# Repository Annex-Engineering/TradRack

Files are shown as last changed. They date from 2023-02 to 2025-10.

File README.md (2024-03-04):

# Trad Rack



Trad Rack is a multimaterial system for FFF printers with a focus on scalability at low cost, developed by Ryan G and the team at Annex Engineering.

Videos of it in action can be found here: 
- [Toolchange and print timelapse (closed beta announcement)](https://youtu.be/wKoVyXH0DT4)
- [Standalone demo (MRRF 2022 preview)](https://youtu.be/hxGiJGAnO-A)

Our discord server can be found here: 

Join me on Discord (https://discord.gg/MzTR3zE)

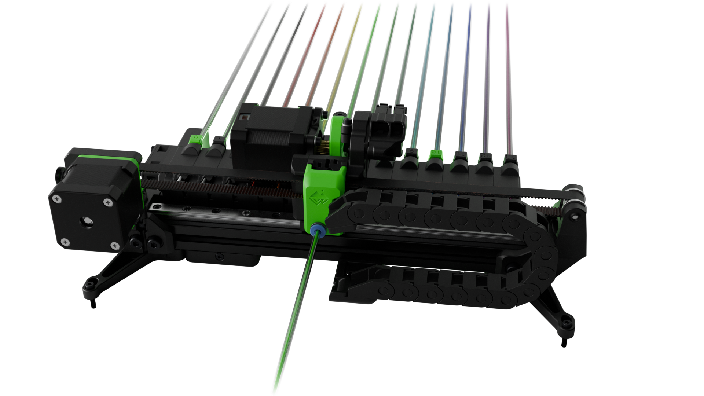
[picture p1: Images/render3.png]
Image of TradRack


## Getting started

See the [Quick Start document](/docs/Quick_Start.md) to get started, or continue
reading below for more general info on Trad Rack.

## Stats

- Single 2020 extrusion as the frame
- Pivoting arm on the selector that lowers a hobbed gear onto the filament, indirectly coupled to a servo through a spring
- MGN9 rail and either 6mm or 9mm 2GT belt for selector movement
- NEMA17 motor for selector movement, and either NEMA17 or 36mm round NEMA14 motor for filament movement

## Scalability

One of the main focuses of Trad Rack is allowing additional filament lanes to be added at the lowest possible cost and assembly/disassembly. Rather than using a separate drive gear (or drive gear pair) for each filament lane, Trad Rack uses a single drive gear pair mounted to the selector for the entire unit. One module is required for each filament lane, and modules can be attached or detached with one screw. Each module consists of the following parts:

- 1X printed module body
- 1X 623 bearing
- 1X M3x8 screw
- 1X M5x10 screw
- 1X M5 T-nut
- 1X bowden fitting

The extrusion, rail, and belt must be long enough to support the selected number of filament lanes, but they can be oversized in order to allow for additional modules to be added later.

## Acknowledgments

- Main filament-switching concept inspired by the [Prusa MMU2](https://github.com/prusa3d/Original-Prusa-i3/tree/MMU2)
- Idea to use a servo to engage/disengage with each filament inspired by the [SMuFF](https://github.com/technik-gegg/SMuFF-1.1)

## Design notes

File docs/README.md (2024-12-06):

# Overview

Welcome to the Trad Rack documentation. If you want to get running as
quickly as possible with minimal reading, see the
[Quick Start document](Quick_Start.md).

## Getting started
- [Quick Start](Quick_Start.md): a step-by-step guide on how to get
  running with Trad Rack.
- [Printer and Hardware Requirements](Printer_and_Hardware_Requirements.md):
  prerequisites for your printer to work with Trad Rack, as well as
  information on other hardware you might need/want to use with Trad
  Rack.

## Assembly and wiring
- [Build Instructions](build_instructions): instructions for
  assembling Trad Rack.
- [Wiring](Wiring.md): information on wiring for Trad Rack.

## Kalico
- [Installation](kalico/Installation.md): how to get Trad Rack set up
  to work with Kalico or Klipper.
- [Config Reference](kalico/Config_Reference.md): config settings for
  Trad Rack.
- [G-Codes](kalico/G-Codes.md): commands added by the trad_rack
  klippy module.
- [Customization](kalico/Customization.md): info on how code is
  divided between the trad_rack klippy module and the config, how to
  customize Trad Rack's behavior through gcode templates, and what the
  trad_rack_optional config file does.
- [Status Reference](kalico/Status_Reference.md): information
  available to macros (and similar) from the trad_rack klippy module.
- [Save Variables](kalico/Save_Variables.md): information on the
  variables that Trad Rack saves to disk using save_variables.

## Tuning and feature overviews
- [Tuning](Tuning.md): overview of the loading and unloading
  processes and information on how to tune them.
- [Tool Mapping](Tool_Mapping.md): info on tool mapping/lane groups
  and how runouts are handled.
- [Tool Naming](Tool_Naming.md): (coming soon)
- [Spoolman Support](Spoolman_Support.md): (coming soon)
- [Extruder Syncing](Extruder_Syncing.md): info on how to use Trad
  Rack as a secondary extruder to reduce load on the printer's main
  extruder, including methods for avoiding error buildup due to
  mismatched extrusion rates.

## Slicing
- [Slicing](slicing/Slicing.md): information on slicing multimaterial
  prints for use with Trad Rack.
- [PrusaSlicer Setup](slicing/PrusaSlicer_Setup.md): instructions for
  using the provided PrusaSlicer profiles, as well as other
  PrusaSlicer-specific slicing info. Make sure to look at the main
  Slicing document first for prerequisites and other info.
- [SuperSlicer Setup](slicing/SuperSlicer_Setup.md): instructions for
  using the provided SuperSlicer profiles, as well as other
  SuperSlicer-specific slicing info. Make sure to look at the main
  Slicing document first for prerequisites and other info.

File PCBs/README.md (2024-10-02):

# TradRack PCBs

The Tradrack-PCBs are a series of PCBs that allow for easier and simpler wiring and troubleshooting on a Trad Rack. They also allow the operator to quickly disconnect the unit from the machine and swap it to another one.

## Boards

| Name | Location |
| --- | --- |
| TR Ebox Distribution | Ebox |
| TR Lower Distribution | Extrusion |
| TR Toolhead | Toolhead |

## Features
The TradRack PCBs have the following features
- 16-pin / 10-pin input/output via MicroFit connector (16-pin to lower distro, 10 pin to toolhead)
- Modular Design
- Dedicated 5V Fused Input (3A Max)
- 1 Aux Expansion ports with power and ground to the Lower Distribution Board
- 3 Aux Expansion ports with power and ground to the Toolhead Board

## Source, PCBs, Gerbers

If you want to help to get the carabiner from any shop that is officially affiliated, please check out the [Annex Sourcing Guide](https://docs.google.com/spreadsheets/d/1O3eyVuQ6M4F03MJSDs4Z71_XyNjXL5HFTZr1jsaAtRc/edit?usp=sharing)

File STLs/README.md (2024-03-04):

# What to print

In general, all parts in the STLs folder need to be printed. However,
there are some exceptions. Some subfolders contain files that you may
not need, and some parts have multiple variants that you can choose
from depending on what hardware you are using.

**Table of Contents**
- [Subfolders that may not be needed](#subfolders-that-may-not-be-needed)
- [STL variants](#stl-variants)
  - [Rail cart variants](#rail-cart-variants)
  - [Belt width variants](#belt-width-variants)
  - [Cable drag chain variants](#cable-drag-chain-variants)

## Subfolders that may not be needed

The following subfolders contain STL files that you may or may not
need to print:

- [Electronics Mounts/Nebula Enclosure](Electronics%20Mounts/Nebula%20Enclosure/):
  these files are only required if you are using the Nebula control
  board. See the
  [Printer and hardware requirements document](/docs/Printer_and_Hardware_Requirements.md#electronics)
  for recommended mounts for other control board options.
- [Electronics Mounts/Base Distribution Board](Electronics%20Mounts/Base%20Distribution%20Board/):
  these files are only required if you are using the optional Trad
  Rack wiring kit.
- [Experimental](Experimental/): experimental parts. These are not
  recommended at this time.
- [Stationary Parts/Numbered Collet Clips](Stationary%20Parts/Numbered%20Collet%20Clips/):
  optional collet clips for labeling the lane modules.
- [Trad Rack Mounts/K3 Side Mount](Trad%20Rack%20Mounts/K3%20Side%20Mount/):
  brackets for mounting Trad Rack to the side of an Annex K3 printer.
  These brackets may also work for mounting Trad Rack to other
  printers or for serving as legs for Trad Rack to sit on a horizontal
  surface. See the
  [Printer and hardware requirements document](/docs/Printer_and_Hardware_Requirements.md#other-recommended-mounts)
  for alternative recommended mounting parts that may work better with
  other printers/setups.

## STL variants

Subfolders containing multiple variants of each part will generally
contain a README file that lists which files you need to print for
each option. The following sections explain file labels that apply to
all STL subfolders in general:

### Rail cart variants

Trad Rack uses an MGN9 rail with either a C-cart or an H-cart. Files
with `(c_cart)` in the filename are only required if using a C-cart.
Files with `(h_cart)` in the filename are only required if using an
H-cart.

### Belt width variants

Trad Rack is compatible with either 6mm or 9mm wide belts (and
pulleys sized for each). Files with `(6mm_belt)` in the filename are
only required if using 6mm wide belts and pulleys/idlers sized for 6mm
belts. Files with `(9mm_belt)` in the filename are only required if
using 9mm wide belts and pulleys/idlers sized for 9mm belts.

### Cable drag chain variants

Cable chains with 10x10mm internal dimensions generally have a 2-hole
mounting pattern for each end, while chains with 10x11mm internal
dimensions generally have a 3-hole mounting pattern. Files with
`(10x10_cable_chain)` in the filename are only required if
using a cable chain with a 2-hole mounting pattern. Files with
`(10x11_cable_chain)` in the filename are only required if using a
cable chain with a 3-hole mounting pattern.

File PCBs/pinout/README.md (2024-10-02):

# Pinout - 16 Pin Harness and 10 Pin Harness

All TR boards (& derivatives) are using a non-standard 16 pin pinout that does not match the carabiner pinout due to alternative power and signaling requirements.

We welcome other groups using the cable for their projects, but kindly ask to note in their project page if they are using the official TR 16 pin pinout, to help prevent damage to users equipment, caused by different pinouts.

## Pinout - 16 Pin Harness

This pinout assumes you're looking directly at the cable. 

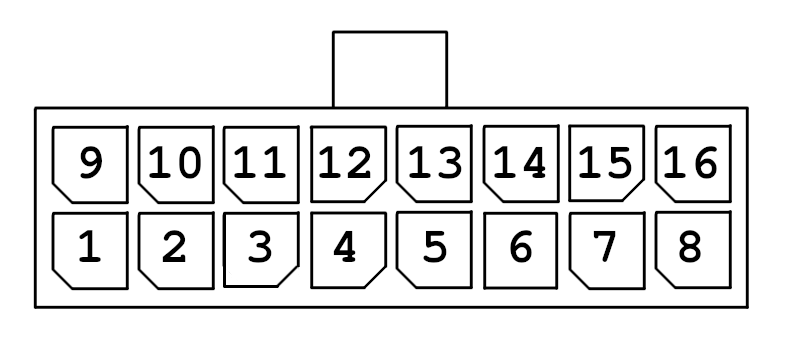
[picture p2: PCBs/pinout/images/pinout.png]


| PinNumber | Usage  | OnPCB | PinNumber | Usage | OnPCB | 
|---|:---:|:---:| --- |:---:|:---:|
| 1  | 5V Input | 5V | 9 | Aux Pin 3 | Aux3
| 2  | Aux Pin 4 | Aux4 | 10 | Aux Pin 2 | Aux2
| 3  | Common Ground | CMN_GND | 11 | Aux Pin 1 | Aux1
| 4  | Feeder End Stop Signal | F_ESTOP_SIGNAL | 12 | Selector End Stop Signal | S_ESTOP_SIGNAL
| 5  | Motor 1 1A | Stepper1A_1 | 13 | Motor 1 2B | Stepper2B_1
| 6  | Motor 1 1B | Stepper1B_1 | 14 | Motor 1 2A | Stepper2A_1
| 7  | Motor 2 1A | Stepper1A_2 | 15 | Motor 2 2B | Stepper2B_2
| 8  | Motor 2 1B | Stepper1B_2 | 16 | Motor 2 2A | Stepper2A_2

## Pinout - 10 Pin Harness

This pinout assumes you're looking directly at the cable. 

| PinNumber | Usage  | OnPCB | PinNumber | Usage | OnPCB | 
|---|:---:|:---:| --- |:---:|:---:|
| 1  | Motor 1 1A | Stepper1A_1 | 6 | Common Ground | CMN_GND 
| 2  | Motor 1 1B | Stepper1B_1 | 7 | 5V Input | 5V
| 3  | Motor 1 2B | Stepper2B_1 | 8 | Aux Pin 3 | Aux3
| 4  | Motor 1 2A | Stepper2A_1 | 9 | Aux Pin 2 | Aux2
| 5  | Feeder End Stop Signal | F_ESTOP_SIGNAL | 10 | Aux Pin 1 | Aux1

## Recommended Wiregauge - 16 Pin Harness

While we have official cables available, we don't want to discourage people making their own cables, as such here is our recommended minimum wiregauge, for making a cable with the official pinout.
These recommendations assume the TR boards are being used in a 50° chamber.

| Pin-Number | Recommended AWG | Recommended mm² |
|:---:|:---:|:---:|
| 1 | 22 | 0.3 |
| 2 | 26 | 0.125 |
| 3 | 22 | 0.3 |
| 4 | 26 | 0.125 |
| 5 | 22 | 0.3 |
| 6 | 22 | 0.3 |
| 7 | 22 | 0.3 |
| 8 | 22 | 0.3 |
| 9 | 26 | 0.125 |
| 10 | 26 | 0.125 |
| 11 | 26 | 0.125 |
| 12 | 26 | 0.125 |
| 13 | 22 | 0.3 |
| 14 | 22 | 0.3 |
| 15 | 22 | 0.3 |
| 16 | 22 | 0.3 |

## Recommended Wiregauge - 10 Pin Harness

While we have official cables available, we don't want to discourage people making their own cables, as such here is our recommended minimum wiregauge, for making a cable with the official pinout.
These recommendations assume the TR boards are being used in a 50° chamber.

| Pin-Number | Recommended AWG | Recommended mm² |
|:---:|:---:|:---:|
| 1 | 22 | 0.3 |
| 2 | 22 | 0.3 |
| 3 | 22 | 0.3 |
| 4 | 22 | 0.3 |
| 5 | 26 | 0.125 |
| 6 | 22 | 0.3 |
| 7 | 22 | 0.3 |
| 8 | 26 | 0.125 |
| 9 | 26 | 0.125 |
| 10 | 26 | 0.125 |

## License

The pinout is licensed under the [MIT license] (https://github.com/git/git-scm.com/blob/main/MIT-LICENSE.txt)

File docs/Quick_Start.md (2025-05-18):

# Quick Start

This document provides an overview of how to get Trad Rack running.
Each section should be completed before moving on to the next.

**Table of Contents**
- [BOM/sourcing and other required hardware](#bomsourcing-and-other-required-hardware)
  - [Item Calculator](#item-calculator)
- [Printing required parts](#printing-required-parts)
- [Mechanical assembly](#mechanical-assembly)
- [Wiring](#wiring)
- [Kalico installation](#kalico-installation)
- [Servo calibration](#servo-calibration)
  - [Servo rotation direction](#servo-rotation-direction)
  - [Servo horn angle](#servo-horn-angle)
  - [Servo up angle](#servo-up-angle)
- [Selector calibration](#selector-calibration)
- [Slicing](#slicing)
- [Changing Slicer\_Unload macro settings](#changing-slicer_unload-macro-settings)
- [First load and unload](#first-load-and-unload)
  - [Setup](#setup)
  - [Loading the toolhead](#loading-the-toolhead)
  - [Unloading the toolhead](#unloading-the-toolhead)
  - [Relevance to print setup](#relevance-to-print-setup)
- [Further reading](#further-reading)

## BOM/sourcing and other required hardware

The bill of materials/sourcing guide for Trad Rack can be found
[here](https://docs.google.com/spreadsheets/d/1SKBtkgSVPqqGEjftI6v6i6T5Bh3Phx-4YXsJYH17ggs/edit?usp=sharing).

Before placing any orders for parts for Trad Rack, it is recommended to read the
[Printer and hardware requirements document](Printer_and_Hardware_Requirements.md)
in case there are any other items you may want to combine into your orders.

### Item Calculator

Several parts of the build are scalable to the needs of the builder. There are two ways to use our item calculator, which can help you determine how many and what sizes of these parts you need.

  - [Web Based Calculator](https://trinket.io/python/694b97d948?outputOnly=true&runOption=run)
  - [Spreadsheet Calculator](https://docs.google.com/spreadsheets/d/1RdqxC5n0PXs8FgdxJVkqQUN2aY69W7eFC76b8XtMozI/edit?usp=sharing)

## Printing required parts

See the following files/folders:

- [Print Settings and File Key](/Print_Settings_and_File_Key.txt):
  print settings to use and info on reading the STL filenames.
- [STLs folder](/STLs): contains all STL files.
- [STLs README](/STLs/README.md): information on what parts to print.

## Mechanical assembly

See the [build instructions](build_instructions) for guidance on
assembling Trad Rack.

> [!TIP]
> An [eDrawing](/eDrawings/) is also available if you want to view a
> 3D model of Trad Rack. You will need
> [eDrawings Viewer](https://www.edrawingsviewer.com/) to open this
> file. If you are using the Nebula control board, a separate eDrawing
> is also available for help on assembling its enclosure.

## Wiring

See the [Wiring document](Wiring.md).

## Kalico installation

See the [Kalico installation document](kalico/Installation.md).

## Servo calibration

This section involves setting the rotation direction and angles of the
servo. You will need to have Trad Rack fully assembled, wired, and
connected to your printer with Kalico running.

To prepare, remove the servo from Trad Rack by undoing the 2 screws
that attach it to the right carriage.

### Servo rotation direction

Run the following gcode command:

```
TR_SERVO_UP
```

Then run the following gcode command, and this time observe the motion
of the servo. When viewed from the front of the servo spline, the 
servo should rotate clockwise:
    
```
TR_SERVO_DOWN FORCE=1
```

If the servo rotated clockwise, you can continue on to setting the
[servo horn angle](#servo-horn-angle). Otherwise, in your Kalico
config, swap the values of `servo_down_angle` and `servo_up_angle` in
the [trad_rack] section. Then restart Kalico and continue.

### Servo horn angle

Run the following gcode command:

```
TR_SERVO_DOWN FORCE=1
```

Loosen the screw in the center of the servo horn and the screw in
the clamp.

For this section, you will need the servo jig that has "HORN ANGLE"
written on the side:

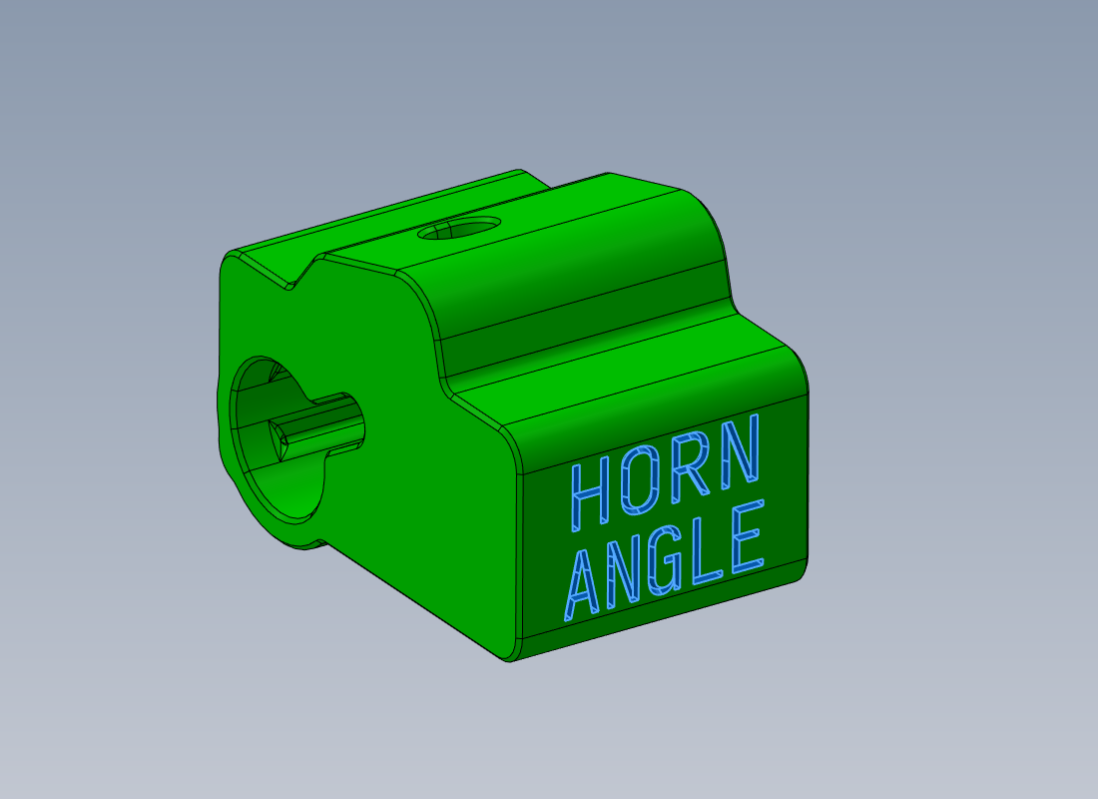
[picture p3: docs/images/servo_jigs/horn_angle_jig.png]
HORN ANGLE servo jig


Insert the servo into the servo jig. You may need to rotate the
servo horn around the servo spline by hand so that it is at the
correct angle for the bearing to fit into the jig. The servo's wires
should be exiting to the left to match the orientation in the image:

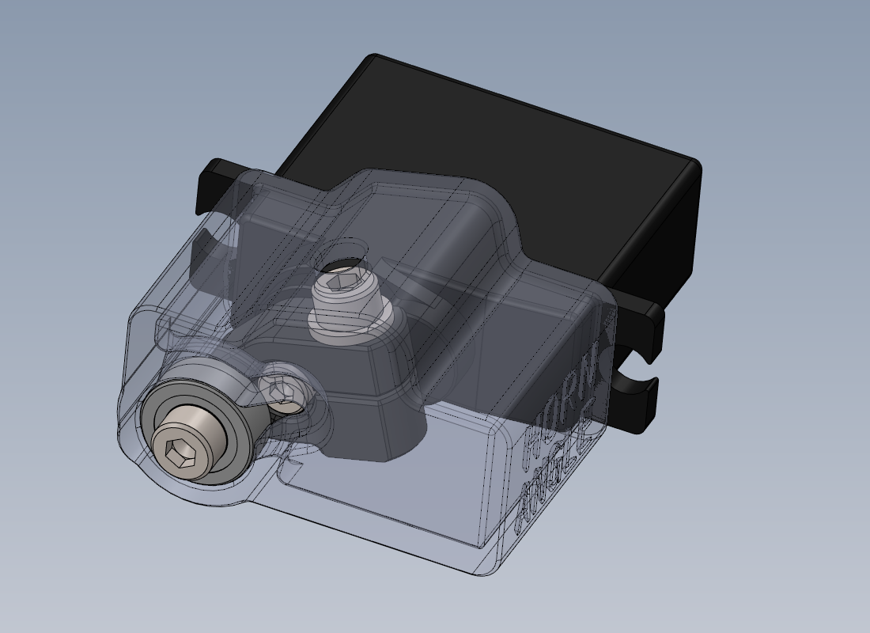
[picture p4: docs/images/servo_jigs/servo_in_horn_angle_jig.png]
Servo in HORN ANGLE jig


Tighten the two screws you loosened earlier. Then remove the servo
jig.

### Servo up angle

For this section, you will need the servo jig that has "UP ANGLE"
written on the side:

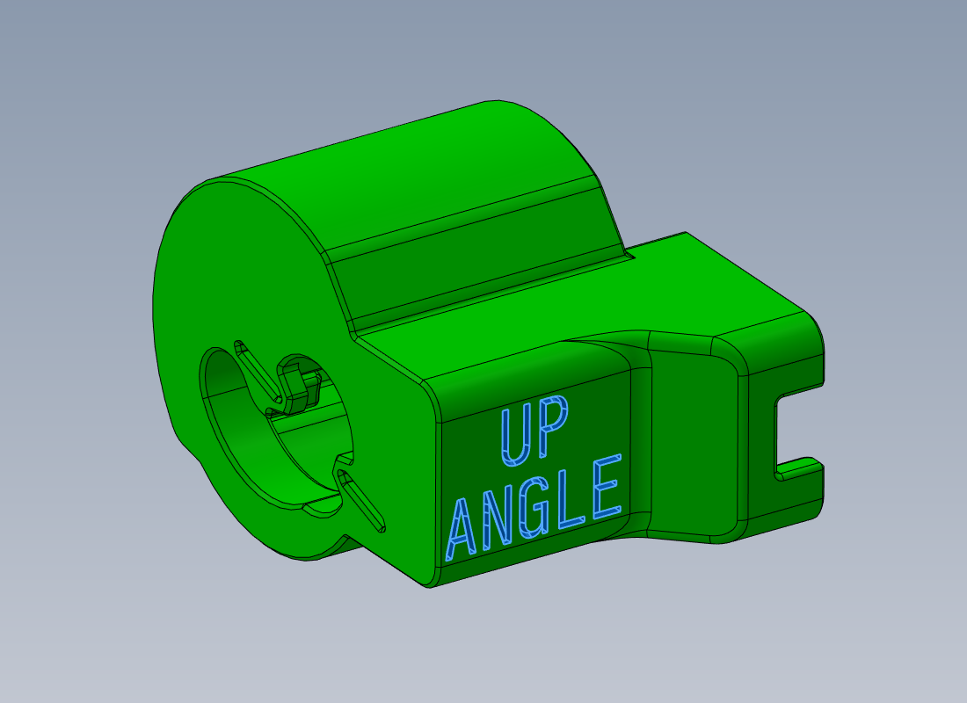
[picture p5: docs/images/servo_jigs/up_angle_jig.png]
UP ANGLE servo jig


Insert the servo into the servo jig. The servo's wires should be
exiting to the left to match the orientation in the image:

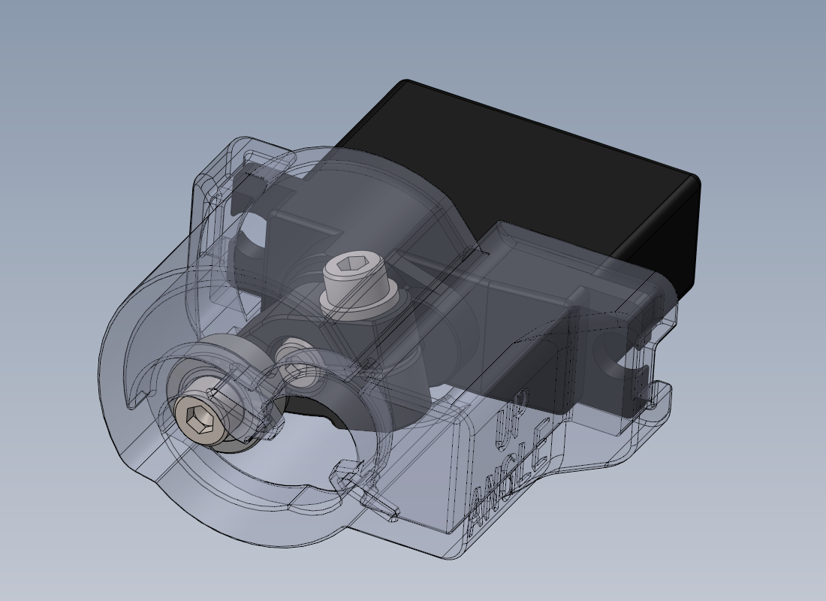
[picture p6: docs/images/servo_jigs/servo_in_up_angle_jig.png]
Servo in UP ANGLE jig


Run the following gcode command. Observe the "commanded angle" that is
reported in the console:

```
TR_SERVO_TEST
```

Look at the front of the servo jig and check the position of the screw
in the bearing relative to the slots. The goal of this section is
to get the screw close to lining up with the slots:

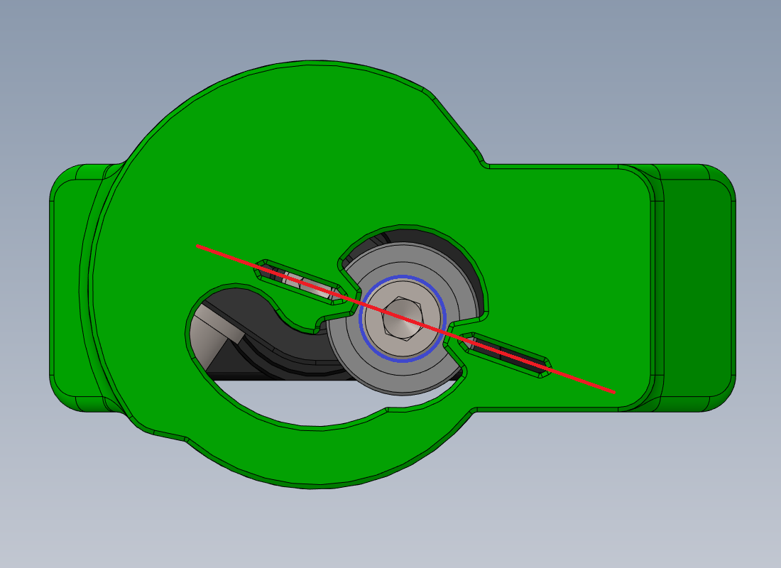
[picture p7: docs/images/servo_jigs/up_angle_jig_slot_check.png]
UP ANGLE servo jig slot check


There is a range of acceptable angles, and the screw does not
have to exactly align with the slots. If the servo angle is within the
target range, the jig will be able to slide far enough over the servo
that the screw protrudes from the front of the jig:

| Wrong angle (screw can't protrude) | Angle within target range (screw protrudes) |
| --- | --- |
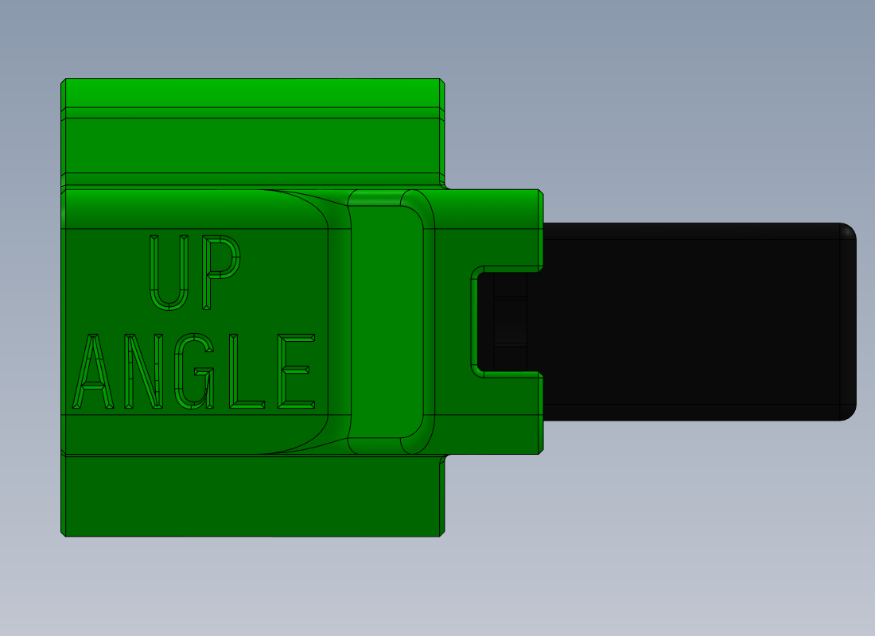
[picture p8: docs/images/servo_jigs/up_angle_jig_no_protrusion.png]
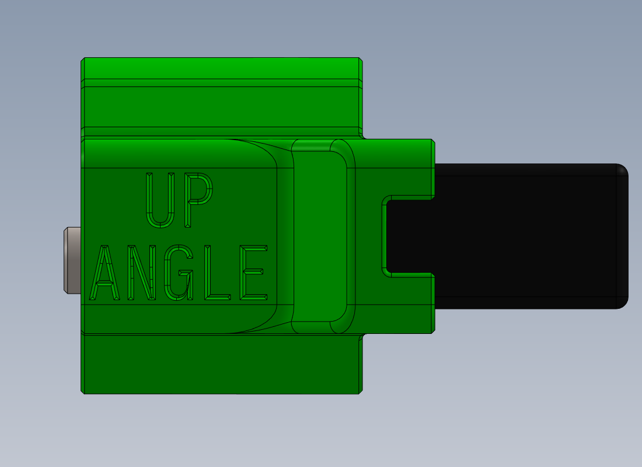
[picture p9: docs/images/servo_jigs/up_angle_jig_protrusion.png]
|   |   |

If the jig is blocked from being able to slide far enough for the
screw to protrude, you will need to try another angle. Use the
following command to test a specific angle. The "commanded angle" from
earlier corresponds to the current angle of the servo. A higher angle
will turn the servo counterclockwise, and a lower angle will turn it
clockwise:

```
TR_SERVO_TEST ANGLE=<angle>
```

Repeat with different angles as necessary until the servo is 
within the target range.

Once the servo aligns well enough with the slots that the screw can
protrude from the jig, observe the last "raw angle" value reported in
the console. In your main Trad Rack config file, replace the value of
`servo_up_angle` in the [trad_rack] section with the "raw angle"
value. Remove the servo jig and restart Kalico. Then run the
following gcode command:

```
TR_SERVO_DOWN FORCE=1
```

Finally, reattach the servo to Trad Rack.

## Selector calibration

This section involves calibrating `lane_spacing`, as well as the min,
endstop, and max positions of the selector motor. You will need access
to filament (either a spool or a short piece is fine).

Run the following gcode command and follow the instructions in the
console:

```
TR_CALIBRATE_SELECTOR
```

When the calibration finishes and you are prompted to do so, replace
the values in your main Trad Rack config file with the new values
for the following:

- in [trad_rack]:
  - `lane_spacing`
- in [stepper_tr_selector]:
  - `position_min`
  - `position_endstop`
  - `position_max`

## Slicing

See the [Slicing document](slicing/Slicing.md).

## Changing Slicer_Unload macro settings

This section involves adjusting the settings of the
[Slicer_Unload macro](kalico/Customization.md#tip-shaping) to match
your slicer settings so that toolhead unloads performed outside of a
print will closely match toolhead unloads performed during a print.

Under `[gcode_macro Slicer_Unload]` in your copy of
[trad_rack_optional.cfg](/Kalico/kalico_config/trad_rack_optional.cfg),
change the values of the following variables to match the values you
set in the slicer profile. Variable names match the "parameter names"
used in the slicer config files:

- all variables under the comment `# printer settings`
- all variables under the comment `# filament settings`

In addition, if you are using SuperSlicer, do the same for all
variables under the comment `# filament settings only in SuperSlicer`.

Set `variable_superslicer` to `True` if you are using SuperSlicer. If
you are using PrusaSlicer or OrcaSlicer, set it to `False`.

Optional: if you want to use different tip-shaping settings for
different filaments (when unloading the toolhead outside of a print),
you can define presets in `[gcode_macro Set_Slicer_Unload_Preset]` in
the same file. See the comments in the macro and the example preset
variables for reference.

## First load and unload

This section goes through the process of running your first toolhead
load and unload to test Trad Rack.

### Setup

Run the following command to home Trad Rack's selector:

```
TR_HOME
```

Get a filament spool ready to feed into Trad Rack. Then run the
following command, and insert the filament into lane module 0 when
prompted to do so in the console:

```
TR_LOAD_LANE LANE=0
```

Trad Rack should now have a filament loaded into lane module 0.

### Loading the toolhead

To load the toolhead from tool 0 (which starts with lane 0 as its
default lane*), run the following command:

```
T0
```

\* see the [G-Codes document](kalico/G-Codes.md#tr_load_toolhead)
for more details on the available parameters for the `TR_LOAD_TOOLHEAD`
and `T<tool index>` toolchange commands.

Depending on your `hotend_load_length` value, filament may or may not
come out of the nozzle.[^1] For the sake of this test, run the
following commands to ensure filament comes out of the nozzle:

```
M83
G1 E10
```

[^1]: It is recommended to set `hotend_load_length` to a value small
enough that filament does not ooze out directly after calling the
toolchange command so that you do not get a blob on the wipe tower.
However, it should not be so small that there are large gaps in the
wipe tower.

### Unloading the toolhead

Run the following command to unload the toolhead. Trad Rack
should retract the filament back into lane module 0:

```
TR_UNLOAD_TOOLHEAD
```

### Relevance to print setup

Congrats, you have completed your first load and unload with Trad
Rack!

When printing with Trad Rack, make sure to load all the filaments you
might need into their lane modules beforehand using the `TR_LOAD_LANE`
command (after ensuring Trad Rack's selector is homed using `TR_HOME`
as needed). It is also possible to load filaments into the lane
modules completely by hand without any gcode commands, but this is
generally not recommended since you will need to make sure the
filament tip is pushed far enough forward that Trad Rack can grab it
but not so far that it blocks selector movement.

It is up to you whether or not to load the first filament to the
toolhead (using `T<tool index>` or `TR_LOAD_TOOLHEAD` commands)
before starting a print. Either way works, as the start gcode in the
slicer will ensure that the first filament gets loaded if it isn't
already.

Whenever you need to unload filament from the toolhead, you can use
the `TR_UNLOAD_TOOLHEAD` command. If a filament is currently loaded
and you want to load a different one, you do not have to call
`TR_UNLOAD_TOOLHEAD` before calling a toolchange command (either
`T<tool index>` or `TR_LOAD_TOOLHEAD`) to load the next filament since
the toolchange command will automatically include the unload as
needed.

## Further reading

This marks the end of the required steps to get Trad Rack running.
See the [Overview document](README.md) to see the full list of
documents available. Some of these were already linked in this guide,
but there are additional ones that provide more information on what
values can be changed for fine tuning, what gcode commands are
available, etc.

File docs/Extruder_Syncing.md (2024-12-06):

# Extruder Syncing

Extruder syncing is an optional feature that syncs Trad Rack's
filament driver to the extruder during printing, as well as during any
extrusion moves within toolhead loading or unloading that would
normally involve only the extruder. It is highly recommended to use
this feature in conjunction with a
[Belay sensor](#belay-extruder-sync-sensor) rather than by itself.

**Table of Contents**
- [Purpose](#purpose)
- [Belay (extruder sync sensor)](#belay-extruder-sync-sensor)
- [Enabling extruder syncing](#enabling-extruder-syncing)

## Purpose

Long filament paths, buffers, or very heavy spools can cause extra resistance
in filament movement, potentially causing the printer's extruder to
struggle. One solution is to use Trad Rack as a secondary extruder in
series with the primary extruder to take some of the load. With
extruder syncing enabled, Trad Rack's filament driver motor is synced
to the primary extruder.

## Belay (extruder sync sensor)

By default, with extruder syncing enabled Trad Rack's filament driver
will be directly synced to the primary extruder. It is not recommended
to use extruder syncing in this way without a sensor since Trad Rack's
filament driver and the primary extruder may gradually drift out of
sync during a long print with no toolchanges or very long extrusion
distances between toolchanges.

The [Belay sensor][1] solves this problem by dynamically
adjusting the `rotation_distance` setting of Trad Rack's filament
driver to keep it in sync with the primary extruder. See
[the Belay repository][1] for details.

[1]: https://github.com/Annex-Engineering/Belay

## Enabling extruder syncing

To enable extruder syncing, set `sync_to_extruder` to `True` in the
[trad_rack config section](kalico/Config_Reference.md#trad_rack).
The [TR_SYNC_TO_EXTRUDER gcode command](kalico/G-Codes.md#tr_sync_to_extruder)
can also be used to enable syncing, and
[TR_UNSYNC_FROM_EXTRUDER](kalico/G-Codes.md#tr_unsync_from_extruder)
can be used to disable syncing. However, any changes made by these
gcode commands will not persist across restarts.

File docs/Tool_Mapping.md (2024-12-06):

# Tool Mapping

This document contains info on tool mapping/lane groups and how
runouts are handled.

By default, each tool or extruder number specified in gcode
corresponds to a lane module on Trad Rack. However, tool numbers can
be decoupled from lane numbers. This allows reassigning a lane to a
tool with a different number and/or assigning a group of lanes to the
same tool.

**Table of Contents**
- [Use cases](#use-cases)
  - [Chaining identical spools together](#chaining-identical-spools-together)
  - [Remapping right before a print](#remapping-right-before-a-print)
- [Slicer and gcode](#slicer-and-gcode)
- [Runouts](#runouts)

## Use cases

Tool mapping has a couple use cases:

### Chaining identical spools together

If you have multiple identical spools of filament, you may want to
swap from one to the next each time one runs out during a print. This
can be accomplished by feeding each spool into a different lane module
in Trad Rack and assigning each of these lanes to the same tool so
that Trad Rack will recognize that they are interchangeable. When
filament from one lane runs out, Trad Rack will automatically initiate
a toolchange to filament from another lane that is assigned to the
same tool, and it will continue the print.

Since you can have as many tools/lane groups as you want (up to the
number of lanes), you can use up old spools while still being able to
print with multiple colors/materials.

### Remapping right before a print

If you already have filaments loaded into Trad Rack and you want to
run a print file that you sliced previously, you don't have to be
restricted to using the same color/material order as what is defined
in the gcode. The tool numbers match the order defined in the gcode,
but you can map whichever lane(s) you want to each tool so that the
correct filament is used for each part of the print.

## Slicer and gcode

The slicer does not need to be aware of the lane groups; it only
tells Trad Rack which tool needs to be loaded. Extruder numbers in the
slicer correspond directly to tool numbers.

Each tool has a default lane that is loaded with every
`TR_LOAD_TOOLHEAD TOOL=<tool index>` or `T<tool index>` command.
Whenever the filament from one lane runs out, another lane in the
tool's lane group will become the new default lane. In addition, if
you load the toolhead with filament from a specific lane using
`TR_LOAD_TOOLHEAD LANE=<lane index>`, that lane will become the new
default lane for its assigned tool.
[Several gcode commands](kalico/G-Codes.md#tool-mapping) are
available for viewing and manipulating the tool mapping/lane
groups.

## Runouts

Whenever Trad Rack detects that the filament has run out (via the
selector filament sensor), it will pause the print, unload the current
filament, and attempt to load new filament from a lane assigned to the
same tool. If successful, it will resume the print automatically. If
unsuccessful, a message will be sent to the console prompting the user
to take action and resume the print manually.

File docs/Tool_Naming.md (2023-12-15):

# Tool Naming

Coming soon. See the `work-name-groups-and-spoolman` branch.

This feature will allow assigning names to tools. Optionally,
toolchanges can be initiated by selecting a name rather than a tool
or lane. For example, the filament profile name in the slicer could
be passed as the name in the toolchange command so that the order of
extruders in the slicer and the order in which filaments are loaded
into trad rack will not matter (as long as the same name is assigned
to a tool). This feature may later tie into
[Spoolman support](Spoolman_Support.md) for automatically assigning
names to tools when a spool ID is assigned to a lane.

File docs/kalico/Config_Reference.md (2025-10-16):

# Trad Rack Configuration reference

This document is modeled after Kalico's
[Config Reference document](https://docs.kalico.gg/Config_Reference.html)
but only contains items pertaining to Trad Rack.

**Table of Contents**
- [Main configuration](#main-configuration)
  - [\[trad\_rack\]](#trad_rack)
- [Additional sections](#additional-sections)
  - [\[stepper\_tr\_selector\]](#stepper_tr_selector)
  - [\[stepper\_tr\_fil\_driver\]](#stepper_tr_fil_driver)
  - [\[tmc2209 stepper\_tr\_selector\]](#tmc2209-stepper_tr_selector)
  - [\[tmc2209 stepper\_tr\_fil\_driver\]](#tmc2209-stepper_tr_fil_driver)
  - [\[servo tr\_servo\]](#servo-tr_servo)

## Main configuration

### [trad_rack]

Main configuration section for Trad Rack. Some config options
reference [Tuning.md](/docs/Tuning.md) for more details.
```
[trad_rack]
selector_max_velocity:
#   Maximum velocity (in mm/s) of the selector. 
#   This parameter must be specified.
selector_max_accel:
#   Maximum acceleration (in mm/s^2) of the selector. 
#   This parameter must be specified.
#filament_max_velocity:
#   Maximum velocity (in mm/s) for filament movement. 
#   Defaults to buffer_pull_speed.
#filament_max_accel: 1500.0
#   Maximum acceleration (in mm/s^2) for filament movement.
#   The default is 1500.0.
toolhead_fil_sensor_pin:
#   The pin on which the toolhead filament sensor is connected.
#   If a pin is not specified, no toolhead filament sensor will 
#   be used.
lane_count:
#   The number of filament lanes. This parameter must be specified.
lane_spacing:
#   Spacing (in mm) between filament lanes. 
#   This parameter must be specified.
#lane_offset_<lane index>:
#   Options with a "lane_offset_" prefix may be specified for any of
#   the lanes (from 0 to lane_count - 1). The option will apply an
#   offset (in mm) to the corresponding lane's position. Lane offsets
#   do not affect the position of any lanes besides the one specified
#   in the option name. This option is intended for fine adjustment
#   of each lane's position to ensure that the filament paths in the
#   lane module and selector line up with each other.
#   The default is 0.0 for each lane.
#lane_spacing_mod_<lane index>:
#   Options with a "lane_spacing_mod_" prefix may be specified for any
#   of the lanes (from 0 to lane_count - 1). The option will apply an
#   offset (in mm) to the corresponding lane's position, as well as
#   any lane with a higher index. For example, if lane_spacing_mod_2
#   is 4.0, any lane with an index of 2 or above will have its
#   position increased by 4.0. This option is intended to account for
#   variations in a lane module that will affect its position as well
#   as the positions of any subsequent modules with a higher index.
#   The default is 0.0 for each lane.
servo_down_angle:
#   The angle (in degrees) for the servo's down position.
#   This parameter must be specified.
servo_up_angle:
#   The angle (in degrees) for the servo's up position.
#   This parameter must be specified.
#servo_wait_ms: 500
#   Time (in milliseconds) to wait for the servo to complete moves
#   between the up and down angles. The default is 500.
selector_unload_length:
#   Length (in mm) to retract a piece of filament out of the selector
#   and back into the lane module after the selector sensor has been
#   triggered or untriggered. This parameter must be specified.
#selector_unload_length_extra: 0.0
#   Extra length (in mm) that is added to selector_unload_length when
#   retracting a piece of filament out of the selector and back into
#   the lane module. After the retraction, the filament is moved
#   forward by this length as well (so this option's value has no
#   effect on the final position of the filament). This option may be
#   useful when using Trad Rack with a motorized spool rewinder that
#   senses tension or compression in the filament between the spool
#   and Trad Rack in order to determine when to rotate the spool. The
#   extra forward movement of the filament after retracting is
#   intended to force the rewinder's sensor to detect tension in the
#   filament, causing rewinding to cease immediately so the filament
#   tip is not moved out of position by excess spool movement. The
#   default is 0.0.
#eject_length: 10.0
#   Length (in mm) to eject the filament into the lane module past the
#   length defined by selector_unload_length. The filament is ejected
#   whenever unloading a depleted spool after a runout to make sure
#   that filament segment is not loaded again until it has been
#   replaced.
bowden_length:
#   Length (in mm) to quickly move filament through the bowden tube
#   between Trad Rack and the toolhead during loads and unloads.
#   See Tuning.md for details. This parameter must be specified.
extruder_load_length:
#   Length (in mm) to move filament into the extruder when loading the
#   toolhead. See Tuning.md for details.
#   This parameter must be specified.
hotend_load_length:
#   Length (in mm) to move filament into the hotend when loading the
#   toolhead. See Tuning.md for details.
#   This parameter must be specified.
toolhead_unload_length:
#   Length (in mm) to move filament out of the toolhead during an
#   unload. See Tuning.md for details. If toolhead_fil_sensor_pin is
#   specified, this parameter must be specified.
#   If toolhead_fil_sensor_pin is not specified, the default is
#   extruder_load_length + hotend_load_length.
#selector_sense_speed: 40.0
#   Speed (in mm/s) when moving filament until the selector
#   sensor is triggered or untriggered. See Tuning.md for details
#   on when this speed is applied. The default is 40.0.
#selector_unload_speed: 60.0
#   Speed (in mm/s) to move filament when unloading the selector.
#   The default is 60.0.
#eject_speed: 80.0
#   Speed (in mm/s) to move the filament when ejecting a filament
#   segment into the lane module.
#spool_pull_speed: 100.0
#   Speed (in mm/s) to move filament through the bowden tube when
#   loading from a spool. See Tuning.md for details. 
#   The default is 100.0.
#buffer_pull_speed:
#   Speed (in mm/s) to move filament through the bowden tube when
#   unloading or loading from a buffer. See Tuning.md for details.
#   Defaults to spool_pull_speed.
#toolhead_sense_speed:
#   Speed (in mm/s) when moving filament until the toolhead
#   sensor is triggered or untriggered. See Tuning.md for details on
#   when this speed is applied. Defaults to selector_sense_speed.
#extruder_load_speed:
#   Speed (in mm/s) to move filament into the extruder when loading
#   the toolhead. See Tuning.md for details. The default is 60.0.
#hotend_load_speed:
#   Speed (in mm/s) to move filament into the hotend when loading the
#   toolhead. See Tuning.md for details. The default is 7.0.
#toolhead_unload_speed:
#   Speed (in mm/s) to move filament when unloading the toolhead.
#   See Tuning.md for details. Defaults to extruder_load_speed.
#load_with_toolhead_sensor: True
#   Whether to use the toolhead sensor when loading the toolhead.
#   See Tuning.md for details. Defaults to True but is ignored if
#   toolhead_fil_sensor_pin is not specified. 
#unload_with_toolhead_sensor: True
#   Whether to use the toolhead sensor when unloading the toolhead.
#   See Tuning.md for details. Defaults to True but is ignored if
#   toolhead_fil_sensor_pin is not specified.
#fil_homing_retract_dist: 20.0
#   Distance (in mm) to retract filament away from a filament sensor
#   before moving on to the next move. This retraction occurs whenever
#   a filament sensor is triggered early during a fast move through
#   the bowden tube. See Tuning.md for details. The default is 20.0.
#target_toolhead_homing_dist:
#   Target filament travel distance (in mm) when homing to the
#   toolhead filament sensor during a load. See Tuning.md for details.
#   Defaults to either 10.0 or toolhead_unload_length, whichever is
#   greater.
#target_selector_homing_dist:
#   Target filament travel distance (in mm) when homing to the
#   selector filament sensor during an unload. See Tuning.md for
#   details. The default is 10.0.
#bowden_length_samples: 10
#   Maximum number of samples that are averaged to set bowden lengths
#   for loading and unloading. See Tuning.md for details. The default
#   is 10.
#load_lane_time: 15
#   Approximate maximum time (in seconds) to wait for filament to
#   reach the selector filament sensor when loading a lane with the
#   TR_LOAD_LANE gcode command. This time starts when the user is
#   prompted to insert filament and determines when the command will
#   be halted early if no filament is detected. The default is 15.
#load_selector_homing_dist:
#   Maximum distance to try to move filament when loading from a lane
#   module to the selector filament sensor before halting the homing
#   move. This value is not used by the TR_LOAD_LANE command but is
#   used in similar scenarios that do not involve user interaction.
#   Defaults to selector_unload_length * 2.
#bowden_load_homing_dist:
#   Maximum distance to try to move filament near the end of a
#   toolhead load (during the slow homing move to the toolhead sensor)
#   before halting the homing move. Defaults to bowden_length.
#bowden_unload_homing_dist:
#   Maximum distance to try to move filament near the end of a
#   toolhead unload (during the slow homing move to the selector
#   sensor) before halting the homing move. Defaults to bowden_length.
#unload_toolhead_homing_dist:
#   Maximum distance to try to move filament near the beginning of a
#   toolhead unload (during the homing move to the toolhead sensor)
#   before halting the homing move.
#   Defaults to (extruder_load_length + hotend_load_length) * 2.
#sync_to_extruder: False
#   Syncs Trad Rack's filament driver to the extruder during printing,
#   as well as during any extrusion moves within toolhead loading or
#   unloading that would normally involve only the extruder.
#   The default is False.
#user_wait_time: 15
#   Time (in seconds) to wait for the user to take an action
#   before continuing automatically. If set to -1, Trad Rack will wait
#   for the user indefinitely. This value is currently used by the
#   TR_LOCATE_SELECTOR gcode command. The default is 15.
#register_toolchange_commands: True
#   Whether to register gcode commands T0, T1, T2, etc. so that they
#   can be used to initiate toolchanges with Trad Rack. If set to
#   False, the TR_LOAD_TOOLHEAD command can still be used as a
#   substitute to initiate toolchanges. The default is True.
#save_active_lane: True
#   Whether to save the active lane to disk whenever it is set using
#   save_variables. If set to True, the TR_LOCATE_SELECTOR gcode
#   command will infer the active lane if the selector filament sensor
#   is triggered and an active lane was saved previously.
#   The default is True.
#keep_servo_down_after_lane_load: False
#   If set to True, after loading filament into a lane the servo is
#   kept down to hold the filament in place. The default is False.
#minimum_cruise_ratio: 0.0
#   See the "printer" section of Kalico's Config Reference document
#   for a description of this parameter. This parameter affects
#   selector moves and filament moves made by Trad Rack. The default
#   is 0.0.
#square_corner_velocity: 0.0
#   See the "printer" section of Kalico's Config Reference document
#   for a description of this parameter. This parameter can affect
#   selector moves and filament moves made by Trad Rack. The default
#   is 0.0.
#log_bowden_lengths: False
#   Whether to log bowden load length data and bowden unload length
#   data (to ~/bowden_load_lengths.csv and ~/bowden_unload_lengths.csv
#   respectively). The default is False.
#pre_unload_gcode:
#   Gcode command template that is run before the toolhead is
#   unloaded. The default is to run no extra commands.
#post_unload_gcode:
#   Gcode command template that is run after the toolhead is
#   unloaded. The default is to run no extra commands.
#pre_load_gcode:
#   Gcode command template that is run before the toolhead is
#   loaded. The default is to run no extra commands.
#post_load_gcode:
#   Gcode command template that is run after the toolhead is
#   loaded. The default is to run no extra commands.
#pause_gcode:
#   Gcode command template that is run whenever Trad Rack needs to
#   pause the print (usually due to a failed load or unload). The
#   default is to run the PAUSE gcode command.
#resume_gcode:
#   Gcode command template that is run whenever the TR_RESUME command
#   needs to resume the print. The default is to run the RESUME
#   gcode command.
```

## Additional sections

### [stepper_tr_selector]

Section for the stepper that moves the selector between lanes.

```
[stepper_tr_selector]
step_pin:
dir_pin:
enable_pin:
rotation_distance:
microsteps:
full_steps_per_rotation:
endstop_pin:
position_min:
position_endstop:
position_max:
#   This should be set to (lane_count - 1) * lane_spacing.
homing_speed:
#   See the "stepper" section in Kalico's Config_Reference.md
#   document for a description of the above parameters.
```

### [stepper_tr_fil_driver]

Section for the stepper that moves filament.

```
[stepper_tr_fil_driver]
step_pin:
dir_pin:
enable_pin:
rotation_distance:
gear_ratio:
microsteps:
full_steps_per_rotation:
endstop_pin:
position_min:
#   This should be set to a large negative number with an absolute
#   value greater than the length of the bowden tube between Trad Rack
#   and the toolhead.
position_endstop: 0
position_max:
#   This should be set to a large positive number greater than the
#   length of the bowden tube between Trad Rack and the toolhead.
homing_positive_dir: False
#   See the "[stepper]" section in Kalico's Config_Reference.md
#   document for a description of the above parameters.
```

### [tmc2209 stepper_tr_selector]

Stepper driver section for stepper_tr_selector.

```
[tmc2209 stepper_tr_selector]
uart_pin:
run_current:
sense_resistor:
#   See the "[tmc_2209]" section in Kalico's Config_Reference.md
#   document for a description of the above parameters. You may have
#   to use a different section name if you use a different driver.
```

### [tmc2209 stepper_tr_fil_driver]

Stepper driver section for stepper_tr_fil_driver.

```
[tmc2209 stepper_tr_selector]
uart_pin:
run_current:
sense_resistor:
#   See the "[tmc_2209]" section in Kalico's Config_Reference.md
#   document for a description of the above parameters. You may have
#   to use a different section name if you use a different driver.
```

### [servo tr_servo]

Section for the servo that moves the drive gear up and down.

```
[servo tr_servo]
pin:
maximum_servo_angle:
minimum_pulse_width:
maximum_pulse_width:
#   See the "[servo]" section in Kalico's Config_Reference.md
#   document for a description of the above parameters.
```

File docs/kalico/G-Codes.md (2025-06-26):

# G-Codes

This document is modeled after Kalico's
[G-Codes document](https://docs.kalico.gg/G-Codes.html) but only
contains items pertaining to Trad Rack.

**Table of Contents**
- [General commands](#general-commands)
  - [TR\_HOME](#tr_home)
  - [TR\_GO\_TO\_LANE](#tr_go_to_lane)
  - [TR\_LOAD\_LANE](#tr_load_lane)
  - [TR\_LOAD\_TOOLHEAD](#tr_load_toolhead)
  - [T0, T1, T2, etc.](#t0-t1-t2-etc)
  - [TR\_UNLOAD\_TOOLHEAD](#tr_unload_toolhead)
  - [TR\_SERVO\_DOWN](#tr_servo_down)
  - [TR\_SERVO\_UP](#tr_servo_up)
  - [TR\_SET\_ACTIVE\_LANE](#tr_set_active_lane)
  - [TR\_RESET\_ACTIVE\_LANE](#tr_reset_active_lane)
  - [TR\_RESUME](#tr_resume)
  - [TR\_LOCATE\_SELECTOR](#tr_locate_selector)
  - [TR\_NEXT](#tr_next)
  - [TR\_SYNC\_TO\_EXTRUDER](#tr_sync_to_extruder)
  - [TR\_UNSYNC\_FROM\_EXTRUDER](#tr_unsync_from_extruder)
- [Calibration and testing](#calibration-and-testing)
  - [TR\_SERVO\_TEST](#tr_servo_test)
  - [TR\_CALIBRATE\_SELECTOR](#tr_calibrate_selector)
  - [TR\_SET\_HOTEND\_LOAD\_LENGTH](#tr_set_hotend_load_length)
  - [TR\_DISCARD\_BOWDEN\_LENGTHS](#tr_discard_bowden_lengths)
- [Tool mapping](#tool-mapping)
  - [TR\_ASSIGN\_LANE](#tr_assign_lane)
  - [TR\_SET\_DEFAULT\_LANE](#tr_set_default_lane)
  - [TR\_RESET\_TOOL\_MAP](#tr_reset_tool_map)
  - [TR\_PRINT\_TOOL\_MAP](#tr_print_tool_map)
  - [TR\_PRINT\_TOOL\_GROUPS](#tr_print_tool_groups)
- [Macros](#macros)

## General commands

### TR_HOME
`TR_HOME`: Homes the selector.

### TR_GO_TO_LANE
`TR_GO_TO_LANE LANE=<lane index>`: Moves the selector to the specified
lane.

### TR_LOAD_LANE
`TR_LOAD_LANE LANE=<lane index> [RESET_SPEED=<0|1>]`: Ensures filament
is loaded into the module for the specified lane by prompting the user
to insert filament, loading filament from the module into the
selector, and retracting the filament back into the module.
If RESET_SPEED is 1, the bowden move speed used for the
specified LANE will be reset to spool_pull_speed from the
[trad_rack config section](Config_Reference.md#trad_rack)
(see [bowden speeds](/docs/Tuning.md#bowden-speeds) for details on how
the bowden speed settings are used). If not specified, RESET_SPEED
defaults to 1.

### TR_LOAD_TOOLHEAD
`TR_LOAD_TOOLHEAD LANE=<lane index>|TOOL=<tool index>
[MIN_TEMP=<temperature>] [EXACT_TEMP=<temperature>]
[BOWDEN_LENGTH=<mm>] [EXTRUDER_LOAD_LENGTH=<mm>]
[HOTEND_LOAD_LENGTH=<mm>]`: Loads filament from the specified lane or
tool into the toolhead*. Either LANE or TOOL must be specified. If
both are specified, then LANE takes precedence. If there is already an
"active lane" because the toolhead has been loaded beforehand, it will
be unloaded before loading the new filament. If `MIN_TEMP` is
specified and it is higher than the extruder's current temperature,
then the extruder will be heated to at least `MIN_TEMP` before
unloading/loading; the current extruder temperature target may be used
instead if it is higher than `MIN_TEMP`, and if not then
[tr_last_heater_target](Save_Variables.md) may be used. If
`EXACT_TEMP` is specified, the extruder will be heated to `EXACT_TEMP`
before unloading/loading, regardless of any other temperature setting.
If any of the optional length parameters are specified, they override
the corresponding settings in the
[trad_rack config section](Config_Reference.md#trad_rack).

\* see the [Tool Mapping document](/docs/Tool_Mapping.md) for
details on the difference between lanes and tools and how they relate
to each other.

### T0, T1, T2, etc.
`T<tool index>`: Equivalent to calling 
`TR_LOAD_TOOLHEAD TOOL=<tool index>`. All of the optional parameters
accepted by the TR_LOAD_TOOLHEAD command can also be used with these
commands.

### TR_UNLOAD_TOOLHEAD
`TR_UNLOAD_TOOLHEAD [MIN_TEMP=<temperature>]
[EXACT_TEMP=<temperature>] [RESET_SPEED=<0|1>]`: Unloads filament from
the toolhead and back into its module. If `MIN_TEMP` is specified and
it is higher than the extruder's current temperature, then the
extruder will be heated to at least `MIN_TEMP` before unloading; the
current extruder temperature target may be used instead if it is
higher than `MIN_TEMP`, and if not then
[tr_last_heater_target](Save_Variables.md) may be used. If
`EXACT_TEMP` is specified, the extruder will be heated to `EXACT_TEMP`
before unloading/loading, regardless of any other temperature setting.
If `RESET_SPEED` is 1, the bowden move speed used for the current lane
will be reset to spool_pull_speed from the
[trad_rack config section](Config_Reference.md#trad_rack)
(see [bowden speeds](/docs/Tuning.md#bowden-speeds) for details on how
the bowden speed settings are used). If not specified, `RESET_SPEED`
defaults to 1.

### TR_SERVO_DOWN
`TR_SERVO_DOWN [FORCE=<0|1>]`: Moves the servo to bring the drive gear
down. The selector must be moved to a valid lane before using this
command, unless FORCE is 1. If not specified, FORCE defaults to 0. The
FORCE parameter is unsafe for normal use and should only be used when
the servo is not attached to Trad Rack's carriage.

### TR_SERVO_UP
`TR_SERVO_UP`: Moves the servo to bring the drive gear up.

### TR_SET_ACTIVE_LANE
`TR_SET_ACTIVE_LANE LANE=<lane index>`: Tells Trad Rack to assume the
toolhead has been loaded with filament from the specified lane. The
selector's position will also be inferred from this lane, and the
selector motor will be enabled if it isn't already.

### TR_RESET_ACTIVE_LANE
`TR_RESET_ACTIVE_LANE`: Tells Trad Rack to assume the toolhead has
not been loaded.

### TR_RESUME
`TR_RESUME`: Completes necessary actions for Trad Rack to recover
(and/or checks that Trad Rack is ready to continue), then resumes the
print if all of those actions complete successfully. For example, if
the print was paused due to a failed toolchange, then this command
would retry the toolchange and then resume the print if the toolchange
completes successfully. You will be prompted to use this command if
Trad Rack has paused the print and requires user interaction or
confirmation before attempting to recover and resume.

### TR_LOCATE_SELECTOR
`TR_LOCATE_SELECTOR`: Ensures the position of Trad Rack's selector is
known so that it is ready for a print. If the user needs to take an
action, they will be prompted to do so and the print will be paused
(for example if the selector sensor is triggered but no active lane is
set). The user_wait_time config option from the
[trad_rack config section](Config_Reference.md#trad_rack) determines
how long Trad Rack will wait for user action before automatically
unloading the toolhead and resuming. In addition, the save_active_lane
config option determines whether this command can infer the "active
lane" from a value saved before the last restart if the selector
filament sensor is triggered but no active lane is currently set.
It is recommended to call this command in the print start gcode.

### TR_NEXT
`TR_NEXT`: You will be prompted to use this command if Trad Rack
requires user confirmation before continuing an action.

### TR_SYNC_TO_EXTRUDER
`TR_SYNC_TO_EXTRUDER`: Syncs Trad Rack's filament driver to the
extruder during printing, as well as during any extrusion moves within
toolhead loading or unloading that would normally involve only the
extruder. See the
[Extruder syncing document](/docs/Extruder_Syncing.md) for more
details. If you want the filament driver to be synced to the extruder
on every startup without having to call this command, you can set
sync_to_extruder to True in the
[trad_rack config section](Config_Reference.md#trad_rack).

### TR_UNSYNC_FROM_EXTRUDER
`TR_UNSYNC_FROM_EXTRUDER`: Unsyncs Trad Rack's filament driver from
the extruder during printing, as well as during any extrusion moves
within toolhead loading or unloading that normally involve only the
extruder. This is the default behavior unless you have set
sync_to_extruder to True in the
[trad_rack config section](Config_Reference.md#trad_rack).

## Calibration and testing

The following commands are used either for calibration or for testing
settings without having to restart Kalico to reload the config.
Calibration procedures that should be run before using Trad Rack are
covered by the [Quick Start document](/docs/Quick_Start.md):

### TR_SERVO_TEST
`TR_SERVO_TEST [ANGLE=<degrees>]`: Moves the servo to the specified
ANGLE relative to the down position. If ANGLE is not specified, the
servo will be moved to the up position defined by servo_up_angle from
the [trad_rack config section](Config_Reference.md#trad_rack).
This command is meant for testing different servo angles in order
to find the correct value for servo_up_angle.

### TR_CALIBRATE_SELECTOR
`TR_CALIBRATE_SELECTOR`: Initiates the process of calibrating
lane_spacing, as well as the min, endstop, and max positions of the
selector motor. You will be guided through the selector calibration
process via messages in the console.

### TR_SET_HOTEND_LOAD_LENGTH
`TR_SET_HOTEND_LOAD_LENGTH VALUE=<value>|ADJUST=<adjust>`: Sets the
value of hotend_load_length, overriding its value from the
[trad_rack config section](Config_Reference.md#trad_rack). Does not
persist across restarts. If the VALUE parameter is used,
hotend_load_length will be set to the value passed in. If the ADJUST
parameter is used, the adjustment will be added to the current value
of hotend_load_length.

### TR_DISCARD_BOWDEN_LENGTHS
`TR_DISCARD_BOWDEN_LENGTHS [MODE=[ALL|LOAD|UNLOAD]]`: Discards saved
values for "bowden_load_length" and/or "bowden_unload_length" (see
[bowden lengths](/docs/Tuning.md#bowden-lengths) for details on how
these settings are used). These settings will each be reset to the
value of `bowden_length` from the
[trad_rack config section](Config_Reference.md#trad_rack), and empty
dictionaries will be saved for
[tr_calib_bowden_load_length and tr_calib_bowden_unload_length](Save_Variables.md).
"bowden_load_length" and tr_calib_bowden_load_length will be
affected if MODE=LOAD is specified, "bowden_unload_length" and
tr_calib_bowden_unload_length will be affected if MODE=UNLOAD is
specified, and all 4 will be affected if MODE=ALL is specified. If not
specified, MODE defaults to ALL.

## Tool mapping

The following gcode commands are used for viewing or manipulating the
tool mapping/lane groups. See the
[Tool Mapping document](/docs/Tool_Mapping.md) for more details:

### TR_ASSIGN_LANE
`TR_ASSIGN_LANE LANE=<lane index> TOOL=<tool index>
[SET_DEFAULT=<0|1>]`:
Assigns the specified LANE to the specified TOOL. If SET_DEFAULT is 1,
LANE will become the default lane for the tool. If not specified,
SET_DEFAULT defaults to 0.

### TR_SET_DEFAULT_LANE
`TR_SET_DEFAULT_LANE LANE=<lane index> [TOOL=<tool index>]`: If TOOL
is specified, LANE will be set as the default lane for the tool. If
TOOL is not specified, LANE will be set as the default lane for its
currently-assigned tool.

### TR_RESET_TOOL_MAP
`TR_RESET_TOOL_MAP`: Resets lane/tool mapping. Each tool will be
mapped to a lane group consisting of a single lane with the same index
as the tool.

### TR_PRINT_TOOL_MAP
`TR_PRINT_TOOL_MAP`: Prints a table of the lane/tool mapping to the
console, with rows corresponding to tools and columns corresponding to
lanes.

### TR_PRINT_TOOL_GROUPS
`TR_PRINT_TOOL_GROUPS`: Prints a list of lanes assigned to each tool
to the console. If a tool has multiple lanes assigned to it, the
default lane will be indicated.

## Macros

In addition to the above gcode commands, the
[trad_rack_optional config file](/Kalico/kalico_config/trad_rack_optional.cfg)
adds several gcode macros (if you choose to include it). See the
[Customization document](Customization.md#macros) for details.

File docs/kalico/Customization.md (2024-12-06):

# Customization

This document contains info on how code is divided between the
[trad_rack klippy module](/Kalico/klippy_module/trad_rack.py)
and the config, how to customize Trad Rack's behavior through gcode
templates, and what the
[trad_rack_optional config file](/Kalico/kalico_config/trad_rack_optional.cfg)
does.

**Table of Contents**
- [Klippy module and config files](#klippy-module-and-config-files)
- [The trad\_rack\_optional config file](#the-trad_rack_optional-config-file)
  - [Main settings](#main-settings)
  - [Tip shaping](#tip-shaping)
    - [When Shape\_Tip is used](#when-shape_tip-is-used)
    - [Contents of the Shape\_Tip macro](#contents-of-the-shape_tip-macro)
  - [Macros](#macros)

## Klippy module and config files

Most of Trad Rack's functionality is handled through the
[trad_rack klippy module](/Kalico/klippy_module/trad_rack.py).
This functionality includes any behaviors that are considered
"universal" enough that they should require no customization besides
simple config value changes, but (hopefully) no more than that. All
other behaviors that may require more extensive customization, such as
filament tip-shaping or cutting procedures, are handled through gcode
templates to allow for more user customization. The following gcode
templates are currently available:

- `pre_unload_gcode`: Gcode command template that is run before the
  toolhead is unloaded. The default is to run no extra commands.
- `post_unload_gcode`: Gcode command template that is run after the
  toolhead is unloaded. The default is to run no extra commands.
- `pre_load_gcode`: Gcode command template that is run before the
  toolhead is loaded. The default is to run no extra commands.
- `post_load_gcode`: Gcode command template that is run after the
  toolhead is loaded. The default is to run no extra commands.
- `pause_gcode`: Gcode command template that is run whenever Trad Rack
  needs to pause the print (usually due to a failed load or unload).
  The default is to run the PAUSE gcode command.
- `resume_gcode`: Gcode command template that is run whenever the
  TR_RESUME command needs to resume the print. The default is to run
  the RESUME gcode command.

## The trad_rack_optional config file

[trad_rack_optional.cfg](/Kalico/kalico_config/trad_rack_optional.cfg)
provides a recommended example implementation of `pre_unload_gcode`
and `post_load_gcode`.[^1] It is highly recommended to include this file
when getting started with Trad Rack; it provides several useful
features, and the [provided slicer profiles](/Slicer_Config/) (as well
as the suggested
[changes to make to existing slicer profiles](/docs/slicing/Slicing.md#changes-to-make-to-existing-profiles))
were made with the assumption that this file is being used. However,
you are encouraged to modify or replace this file to fit your needs.

[^1]: `post_unload_gcode`, `pre_load_gcode`, `pause_gcode`, and
`resume_gcode` are left at their default values.

### Main settings

`[gcode_macro TR_Variables]` contains several variables that allow for
quick customization. This includes adjusting positions as well as
enabling or disabling features. See the comments next to these
variables for more details.

### Tip shaping

`[gcode_macro Shape_Tip]` is used for shaping the tip of the filament
before unloading. This can include mimicing ramming and unload
behavior from the slicer, filament cutting, etc. 

#### When Shape_Tip is used

By default, the `Shape_Tip` macro is called in `pre_unload_gcode`
before unloading *only if a print is not in progress* (since it is
assumed that your print gcode file will contain tip-shaping gcode of
its own). It is also possible to use the `Shape_Tip` macro during a
print; see the
[Slicing document](/docs/slicing/Slicing.md#experimental-options) for
more details.

#### Contents of the Shape_Tip macro

By default, the `Shape_Tip` macro will call `Slicer_Unload`. This is
another macro defined in
[trad_rack_optional.cfg](/Kalico/kalico_config/trad_rack_optional.cfg)
that mimics ramming and/or unload behavior from PrusaSlicer or
SuperSlicer. If you want the `Shape_Tip` macro to do something else
instead (for example if you are using a filament cutter and don't need
the typical tip-shaping procedure), you can replace the call to
`Slicer_Unload` with something else.

### Macros

[trad_rack_optional.cfg](/Kalico/kalico_config/trad_rack_optional.cfg)
adds the following macros. See the comments in the file for
information on how these macros are meant to be used and what
parameters they expect:

- `TR_Variables`: Contains variables for quick customization of
  `pre_unload_gcode` and `post_load_gcode`. See
  [main settings](#main-settings).

- `Shape_Tip`: Macro that gets called in `pre_unload_gcode` whenever
  Trad Rack inserts its own gcode for tip-shaping. See
  [tip shaping](#tip-shaping).

- `Set_Slicer_Unload_Preset`: Applies setting presets for
  the `Slicer_Unload` macro. Presets can be defined by creating new
  variables in `[gcode_macro Set_Slicer_Unload_Preset]`.

- `Slicer_Unload`: Mimics the ramming and/or unload
  behavior of PrusaSlicer or SuperSlicer. Settings can be adjusted
  by directly adjusting the macro's variables or by using
  `Set_Slicer_Unload_Preset`. Most variable names match the "parameter
  names" used in the slicer.

- `_Wait_for_Toolchange_Temp`: Helper macro for `Slicer_Unload`.

- `Home_and_Wipe_Nozzle`: Used in `pre_unload_gcode` (if
  `variable_use_wiper` is set to `True` in
  `[gcode_macro TR_Variables]`). See the comment in
  `[gcode_macro TR_Variables]` next to `variable_use_wiper` for more
  details.

- `Save_Pressure_Advance`: Saves the current pressure advance value so
  that it can be restored after tip-shaping. See the
  [Slicing document](/docs/slicing/Slicing.md#print-settings) for how
  this macro is meant to be used. This macro may be useful if you set
  pressure advance only at the start of a print.

- `Restore_Pressure_Advance`: Used by `post_load_gcode` to restore the
  pressure advance value saved by `Save_Pressure_Advance` after a
  toolchange.

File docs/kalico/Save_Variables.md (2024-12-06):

# Save Variables

Trad Rack uses
[save_variables](https://docs.kalico.gg/Config_Reference.html#save_variables)
to save variables to disk so that they can be used across restarts.
This document lists all of the variables that Trad Rack saves to disk.

## Bowden lengths

The following variables are used for storing bowden length data,
which is used to set "bowden_load_length" and "bowden_unload_length"
after a restart. See the
[Tuning document](/docs/Tuning.md) for details on how
"bowden_load_length" and "bowden_unload_length" are used:

- `tr_calib_bowden_load_length`: Dict containing the following bowden
  load length data. This variable is saved each time the toolhead is
  loaded[^1]:
  - `new_set_length`: The last calibrated "bowden_load_length".
  - `sample_count`: The number of samples that were averaged to
    determine `new_set_length`.
- `tr_calib_bowden_unload_length`: Dict containing the following
  bowden unload length data. This variable is saved each time the
  toolhead is unloaded:
  - `new_set_length`: The last calibrated "bowden_unload_length".
  - `sample_count`: The number of samples that were averaged to
    determine `new_set_length`.
- `tr_config_bowden_length`: The value of `bowden_length` at the time
  that bowden length data was last saved. On a restart, the saved
  bowden length data will be ignored if `bowden_length` does not match
  `tr_config_bowden_length`. This variable is saved each time Kalico
  starts.

[^1]: If `toolhead_fil_sensor_pin` is not specified or
`load_with_toolhead_sensor` is False, `tr_calib_bowden_load_length`
will not be saved.

## Other variables

The following miscellaneous variables are saved:

- `tr_last_heater_target`: Extruder target temperature that was set by
  the user the last time the toolhead was loaded. This variable may be
  used by the
  [TR_LOAD_TOOLHEAD or TR_UNLOAD_TOOLHEAD gcode commands](G-Codes.md)
  for setting the extruder temperature before unloading/loading. This
  variable is saved each time the toolhead is loaded.
- `tr_active_lane`: Last "active lane" (lane from which filament is
  currently loaded in the toolhead). If `save_active_lane` is set to
  True in the 
  [trad_rack config section](Config_Reference.md#trad_rack),
  then this variable is saved whenever the active lane is set (when
  the toolhead is loaded or unloaded, when the active lane is manually
  set or reset, etc.). If `save_active_lane` is True and this variable
  is not None, the variable will be used by the
  [TR_LOCATE_SELECTOR gcode command](G-Codes.md#tr_locate_selector) to
  infer the active lane if the selector filament sensor is triggered
  but no active lane was set since the last restart.

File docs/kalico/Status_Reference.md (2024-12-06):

# Status Reference

This document is modeled after Kalico's
[Status Reference document](https://docs.kalico.gg/Status_Reference.html)
but only contains items pertaining to Trad Rack.

## trad_rack

The following information is available in the `trad_rack` object:
- `curr_lane`: The lane the selector is currently positioned at.
- `active_lane`: The lane currently loaded in the toolhead.
- `next_lane`: The next lane to load to the toolhead if a toolchange
  is in progress.
- `next_tool`: The next tool to load to the toolhead if a toolchange
  is in progress (if a tool number was specified for the toolchange).
- `tool_map`: An array of integers listing the assigned tool for each
  lane. The tool number for a specified lane can be accessed with
  `tool_map[<lane index>]`.
- `selector_homed`: Whether or not the selector axis is homed.

## save_variables

Trad Rack uses the `save_variables` object to save variables to disk
so that they can be used across restarts. See the
[Save Variables document](Save_Variables.md) for more details
on how Trad Rack uses save_variables, and Kalico's
[Command Templates document](https://docs.kalico.gg/Command_Templates.html#save-variables-to-disk)
for details on how to access all saved variables.

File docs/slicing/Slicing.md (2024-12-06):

# Slicing

This document explains how to get your slicer set up for multimaterial
printing with Trad Rack. These instructions are mainly geared towards
PrusaSlicer and SuperSlicer, but some parts may be relevant to other slicers
(such as OrcaSlicer) that are based on Slic3r and PrusaSlicer.

**Table of Contents**
- [Provided slicer profiles](#provided-slicer-profiles)
  - [Prerequisites](#prerequisites)
  - [Setup](#setup)
  - [Experimental options](#experimental-options)
- [Changes to make to existing profiles](#changes-to-make-to-existing-profiles)
  - [Printer settings](#printer-settings)
    - [Common settings](#common-settings)
    - [Toolhead-specific settings](#toolhead-specific-settings)
  - [Print settings](#print-settings)
  - [Filament settings](#filament-settings)

## Provided slicer profiles

Example slicer profiles are provided for PrusaSlicer and SuperSlicer.
These profiles are meant for use with a K3 running a Sherpa Micro
extruder and Mosquito Magnum hotend, but they can be modified to fit
other setups.

### Prerequisites

These profiles assume you have included
[trad_rack_optional.cfg](/Kalico/kalico_config/trad_rack_optional.cfg)
in your Kalico config and that you have a `Print_Start` g-code macro
that takes the following parameters:

- `EXTRUDER`: Hotend temperature
- `BED`: Bed temperature

### Setup

See the [PrusaSlicer_Setup](PrusaSlicer_Setup.md) or 
[SuperSlicer_Setup document](SuperSlicer_Setup.md) for information on
adding the provided profiles to your slicer, as well as any setup tips
that pertain to that slicer specifically. In addition, if you are
using a different printer or toolhead setup, you may need to change
values in the "Single extruder multimaterial parameters" and
"Toolchange parameters with single extruder MM printers" sections in
the slicer. See
[toolhead-specific settings](#toolhead-specific-settings) and
[filament settings](#filament-settings) for more details on these
settings.

### Experimental options

Experimental profiles are included that eliminate the ramming and/or
unload gcode generated by the slicer in favor of using gcode or macros
called by the toolchange command: print profiles with "No Unload" and
filament profiles with "No Ramming" in their name. You must
select a printer profile with "Experimental" in its name to allow
these print and/or filament profiles to be selected.

In addition, if you use a "No Unload" print profile, you must modify
`post_process` depending on where you have Python installed and where
[remove_unload.py](/Slicer_Scripts/remove_unload.py) is located on
your computer. You can do this either in the slicer or by directly
editing the `Annex_K3_TR.ini` file in a text editor. If you choose to
edit `Annex_K3_TR.ini`, keep in mind that special characters such as
`"` and `\` must be escaped with a backslash. For example, here is the
setting I use, shown in the slicer:

Plater: select profiles

And in the .ini file:

```ini
[print:*No Unload*]
post_process = "\"C:\\Users\\Ryan\\AppData\\Local\\Programs\\Python\\Python310\\python.exe\" \"C:\\Users\\Ryan\\Documents\\3d printing stuff\\TradRack_Beta\\Slicer_Scripts\\remove_unload.py\""
```

If you don't know where you have Python installed, you can use the
following command in the terminal to get the path:

```shell
python -c "import sys; print(sys.executable)"
```

If the above command doesn't work, try using `python3` instead of
`python`.

The script requires the following slicer settings in your filament
profile(s) to work:
- set `filament_unloading_speed_start` to `100`
- make sure your `end_filament_gcode` starts with the comment
  `; Filament-specific end gcode`

With the ramming and/or unload gcode removed, you will need to have
some sort of replacement run in the `pre_unload_gcode` in the
[trad_rack] section of your Kalico config. The simplest way to do
this (assuming you have included
[trad_rack_optional.cfg](/Kalico/kalico_config/trad_rack_optional.cfg))
is to set `variable_shape_tip` to `True` in the
[gcode_macro TR_Variables] section. Keep in mind that the provided
`Shape_Tip` macro includes both ramming and unloading.

## Changes to make to existing profiles

This section explains changes to make to an existing single-tool
slicer profile. Setting names used here follow the "parameter names"
that are used in the slicer config files; you can use the search
function to see which settings these correspond to in the GUI.

### Printer settings

The following changes should be made to the printer config file in the
Printer Settings tab:

#### Common settings

- `extruders_count`: Set this to the number of lanes.
- `single_extruder_multi_material`: Set to `true` (`1` in the config).
- `start_gcode`:
  - Add the following lines to the beginning of the Start G-code
    section:
    
    ```
    CLEAR_PAUSE
    TR_LOCATE_SELECTOR
    T{initial_tool} MIN_TEMP={first_layer_temperature[initial_tool]}
    ```
    
    Explanation:
    - `CLEAR_PAUSE`: Clears the paused state.
    - `TR_LOCATE_SELECTOR`: See the
      [G-Codes document](/docs/kalico/G-Codes.md/#tr_locate_selector)
      for more details.
    - `T{initial_tool} MIN_TEMP={...}`: Loads the first filament into
      the toolhead.
  - Usually not required: if any g-code command or macro that gets
    called within your Start G-code section contains the `M18` or
    `M84` command, add the following to the end of
    the Start G-code section:
    
    ```
    TR_SET_ACTIVE_LANE LANE={initial_tool}
    ```

    > [!NOTE]
    > This includes commands that are called indirectly. For example,
    > if the Start G-code section contains `Print_Start` and your
    > `Print_Start` macro calls `G28`, and your config includes a
    > \[homing_override\] section that causes `G28` to call `M18` or
    > `M84`, this would still count.

    Explanation:
    - The `M18` or `M84` command disables all motors on the printer,
      including Trad Rack's motors. This will cause problems the next
      time Trad Rack tries to move its selector. Normally it is a bad
      idea to disable the motors inside your start g-code. However,
      it is sometimes used as a workaround in the \[homing_override\]
      section in order to allow the printer to move an axis without
      marking that axis as homed. For example, you may want to lift
      the z axis before homing x and y to ensure the nozzle does not
      scrape on the bed. If you do not want to remove `M18` or `M84`
      from the command or macro that is being called in your Start
      G-code section, the `TR_SET_ACTIVE_LANE` command can be used as
      shown above to force Trad Rack to set the selector's position
      without homing it again.
- `retract_length_toolchange`: Set to `0` for all extruders.

#### Toolhead-specific settings

- `cooling_tube_retraction`: Distance between the nozzle tip and the
  center of the "cooling tube." The cooling tube should start somewhere
  above the heatbreak throat and end somewhere below the extruder
  gears. I recommend having the top end below the top of the heatsink,
  but it can extend further if you wish (more experimentation needed).
  Note that the slicer recommends using the extruder/nozzle tip as the
  starting point, but the filament tip will likely break away from the
  molten filament above that point when unloading.
- `cooling_tube_length`: See the above explanation for
  `cooling_tube_retraction`.

  See the drawing below for a visualization of the cooling tube settings.
  Colorful labels are slicer settings, and black labels in
  parentheses are references that are used to determine the starting
  or ending points of the slicer settings.

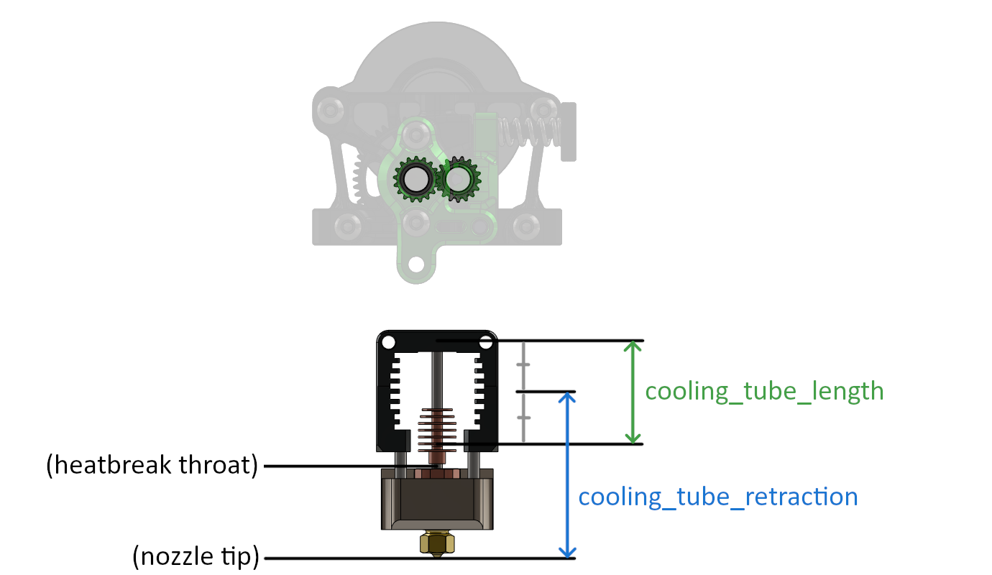
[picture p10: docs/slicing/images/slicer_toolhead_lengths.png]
  

- `parking_pos_retraction`: Set this to 
  `cooling_tube_retraction + cooling_tube_length / 2`.
- `extra_loading_move`: Set this to a negative number with an
  absolute value slightly less than that of `parking_pos_retraction`.
  For example, if `parking_pos_retraction` is `37`, set this to
  `-36.99`.
- Advanced wipe tower purge volume calculs:
  - In SuperSlicer, one of the options for purge volume calculations
    is to have the slicer calculate volumes based on each filament's
    pigment percentage. See the tooltips[^1] for more details on these
    settings:
    - `wipe_advanced`
    - `wipe_advanced_nozzle_melted_volume`
    - `wipe_advanced_multiplier`
    - `wipe_advanced_algo`

### Print settings

The following changes should be made to the print config file in the
Print Settings tab:

- `wipe_tower`: set to `true` (`1` in the config) unless you are using
  an alternative way of purging material.
- `single_extruder_multi_material_priming`: set to `false` (`0` in the
  config).
- `only_retract_when_crossing_perimeters`: set to `false` (`0` in the
  config) to avoid colors bleeding into each other when the nozzle
  moves over the print.
- `gcode_substitutions`[^2]:
  - PrusaSlicer:
    - in the config file:

      ```ini
      gcode_substitutions = "(SET_PRESSURE_ADVANCE ADVANCE=[0.]+)\\n";"Save_Pressure_Advance\\n${1}\\n";r;"Save PA before ramming"
      ```

    - or in the GUI:
      
      PrusaSlicer gcode_substitutions

      - Find: `(SET_PRESSURE_ADVANCE ADVANCE=[0.]+)\n`
      - Replace with: `Save_Pressure_Advance\n${1}\n`
      - Notes: `Save PA before ramming`
      - Make sure "Regular expression" is checked!    

  - SuperSlicer:
    - in the config file:

      ```ini
      gcode_substitutions = "(SET_PRESSURE_ADVANCE ADVANCE=[0.]+)(?: EXTRUDER=extruder[0-9]*)?\\n";"Save_Pressure_Advance\\n${1}\\n";r;"See: https://github.com/supermerill/SuperSlicer/issues/2934 (3073 too)"
      ```

    - or in the GUI:

      SuperSlicer gcode_substitutions

      - Find: `(SET_PRESSURE_ADVANCE ADVANCE=[0.]+)(?: EXTRUDER=extruder[0-9]*)?\n`
      - Replace with: `Save_Pressure_Advance\n${1}\n`
      - Notes: `See: https://github.com/supermerill/SuperSlicer/issues/2934 (3073 too)`
      - Make sure "Regular expression" is checked!

[^2]: These substitutions are required if you only set the pressure
advance value at the start of the print. If you set the pressure
advance value in your `start_filament_gcode` for each filament, then
the substitutions are unnecessary (but there is no harm in having
both).

### Filament settings

The following filament parameters are relevant to multimaterial
printing. See the tooltips[^1] for more details on these settings:

- `filament_loading_speed_start`
- `filament_loading_speed`
- `filament_unloading_speed_start`
- `filament_unloading_speed`
- `filament_load_time`
- `filament_unload_time`
- `filament_toolchange_delay`
- `filament_cooling_moves`
- `filament_cooling_initial_speed`
- `filament_cooling_final_speed`
- `filament_ramming_parameters`

With the toolhead-specific printer parameters set as described in
[toolhead-specific settings](#toolhead-specific-settings),
`filament_loading_speed` has no effect and
`filament_loading_speed_start` has almost no effect since it is only
used for a move with close to 0 length. For the rest of the settings,
I recommend starting either with values from the
[provided slicer profiles](/Slicer_Config/) or with values from
[Prusa's MMU filament profiles](https://github.com/prusa3d/PrusaSlicer/blob/master/resources/profiles/PrusaResearch.ini). The optimal values for each of
these parameters may depend on your hotend and/or filament.

[^1]: In the slicer GUI, hover the mouse cursor over a parameter's
textbox/checkbox to make the tooltip appear.

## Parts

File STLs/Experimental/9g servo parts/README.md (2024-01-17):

# 9g servo parts

The parts in this folder allow using a 9g/SG90 servo in place of the FEETECH MINI FT1117M. A metal gear servo is recommended.

## Replaced parts

The parts in this folder replace the following parts:

- STLs:
  - Selector:
    - `microfit_holder_x1`
    - `carriage_right_x1`
    - `servo_horn_x1`

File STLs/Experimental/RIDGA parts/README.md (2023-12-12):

# RIDGA parts

The parts in this folder allow using the BMG Reverse Integrated Drive
Gear Assembly (RIDGA) in place of the 50T spur/shaft and drive
gear, with 4x8x3.0mm bearings in place of the 5x8x2.5mm ones normally
used with the BMG.

These parts are meant for use with RIDGA V1. If you are using RIDAGA
V2, you can use the normal parts instead of the ones from this folder.

## Replaced parts

The parts in this folder replace the following parts:

- STLs:
  - Selector:
    - `carriage_left_x1`
  - Tilting Filament Driver:
    - `motor_plate_x1`

## eDrawing/Instructions

Until this option gets its own configuration in the eDrawing, you can
use the default configuration for reference but with the following
changes:

- omit the 0.5mm shim next to the drive gear
- optional: omit the `nema_17_spacer_x1` printed part

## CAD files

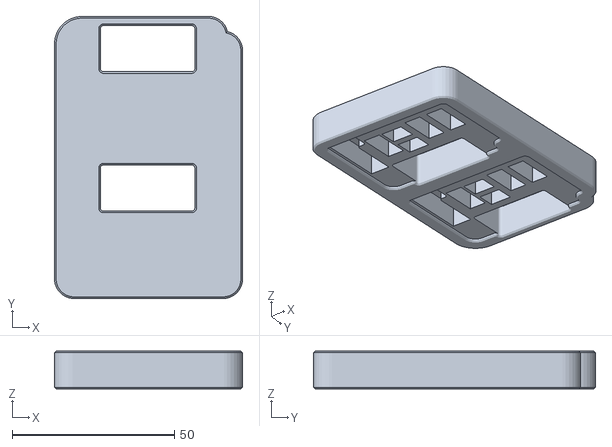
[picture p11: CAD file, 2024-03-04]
PCBs/Assembly_Jigs/TR_ebox_distro_flat.STL
58.0 x 87.0 x 11.7

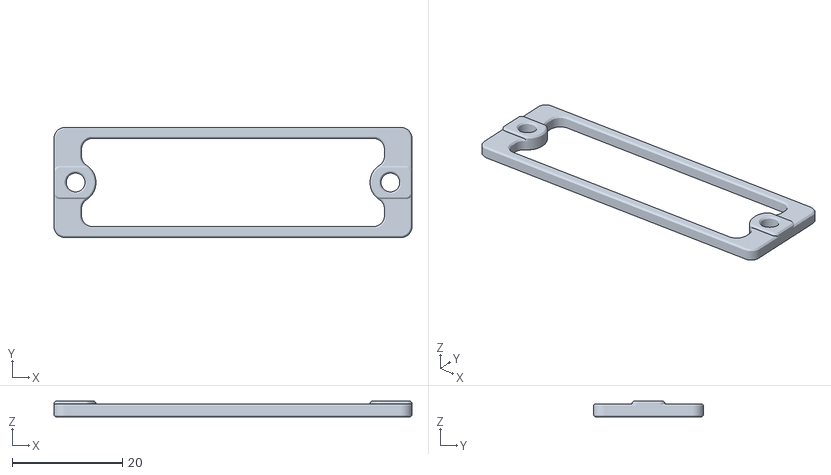
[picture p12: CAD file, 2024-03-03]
STLs/Electronics Mounts/Base Distribution Board/spacer_base_distribution_board_rev1.STL
65.0 x 20.0 x 2.90

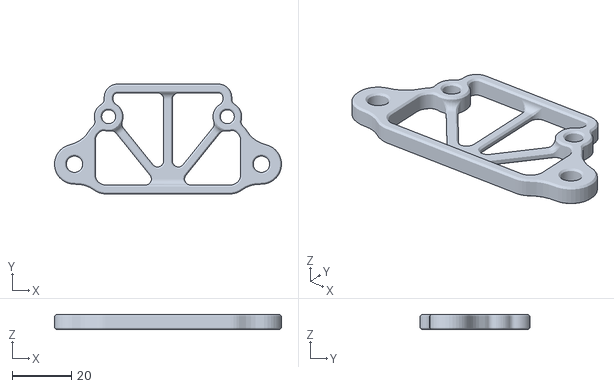
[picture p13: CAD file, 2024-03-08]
STLs/Electronics Mounts/eBox Board/carabiner_distribution_mounting_bracket_x1_rev1.STL
76.5 x 37.0 x 5.00

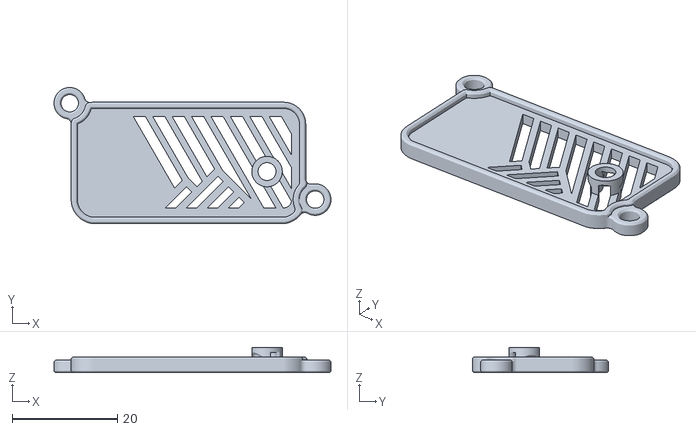
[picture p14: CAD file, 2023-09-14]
STLs/Electronics Mounts/Nebula Enclosure/[a]_finger_guard_x1_rev1.STL
52.7 x 25.9 x 4.80

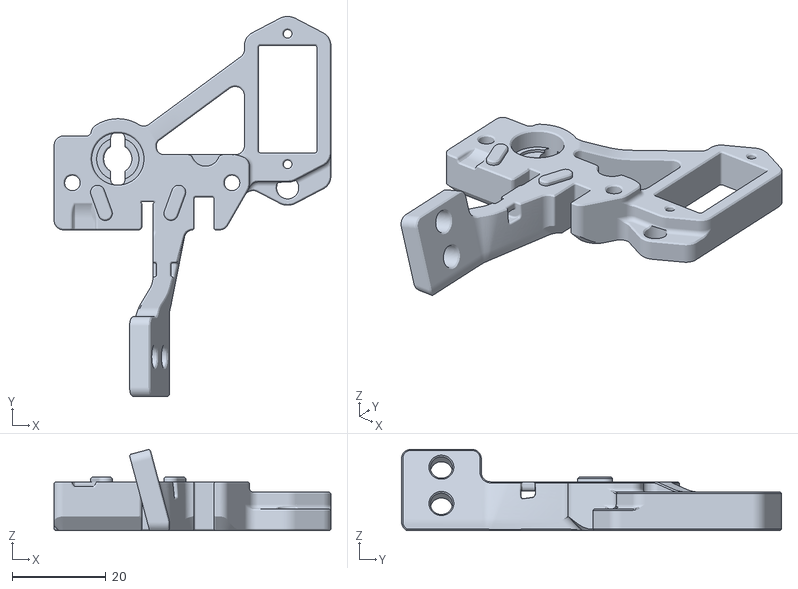
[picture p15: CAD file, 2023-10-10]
STLs/Experimental/9g servo parts/carriage_right_(9g_servo)_x1_rev4.STL
59.0 x 80.9 x 17.3

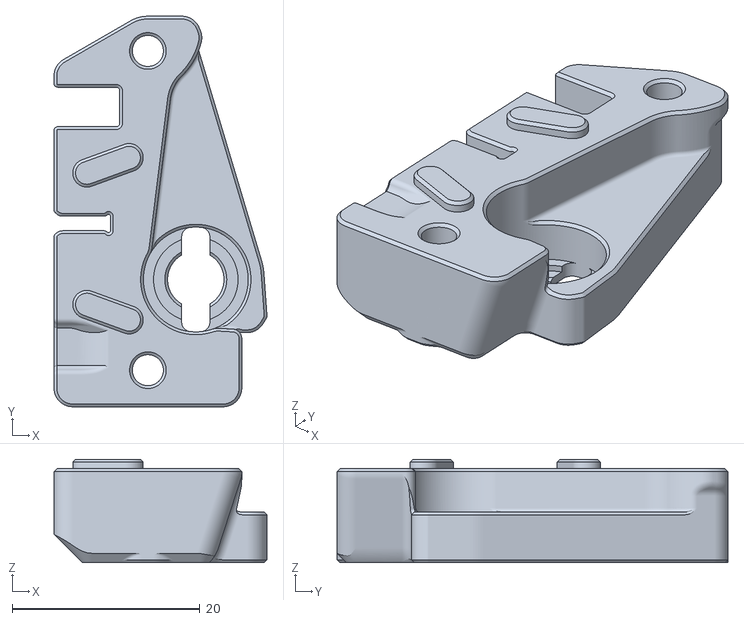
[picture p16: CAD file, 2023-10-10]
STLs/Experimental/RIDGA parts/carriage_left_(ridga)_x1_rev3.STL
22.7 x 41.6 x 11.0

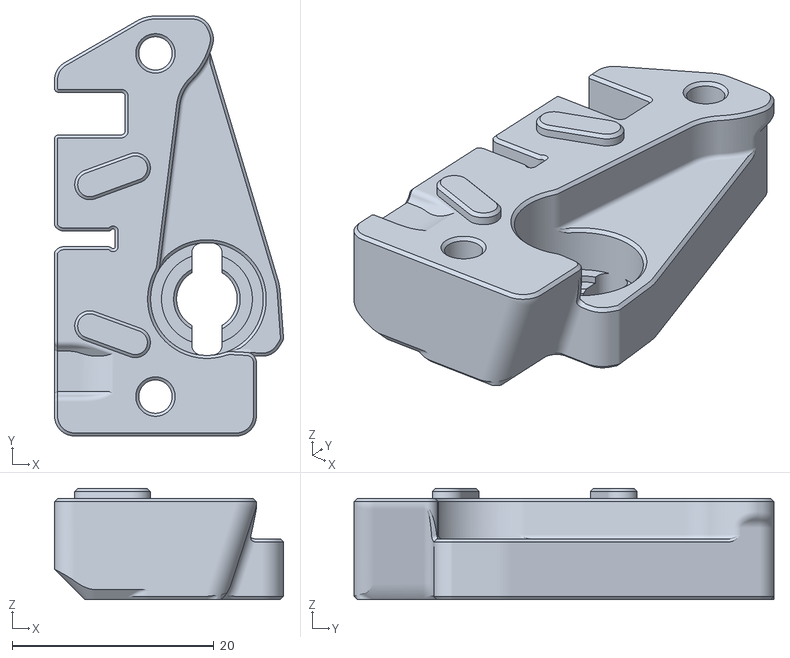
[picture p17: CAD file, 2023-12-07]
STLs/Selector/carriage_left_x1_rev7.STL
22.7 x 41.6 x 11.0

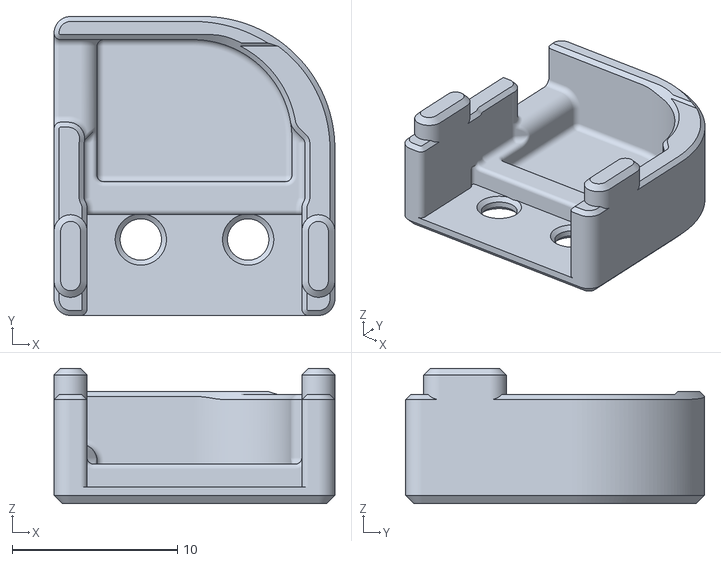
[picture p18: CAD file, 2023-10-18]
STLs/Stationary Parts/[a]_endstop_cover_x1_rev3.STL
17.0 x 18.1 x 8.20

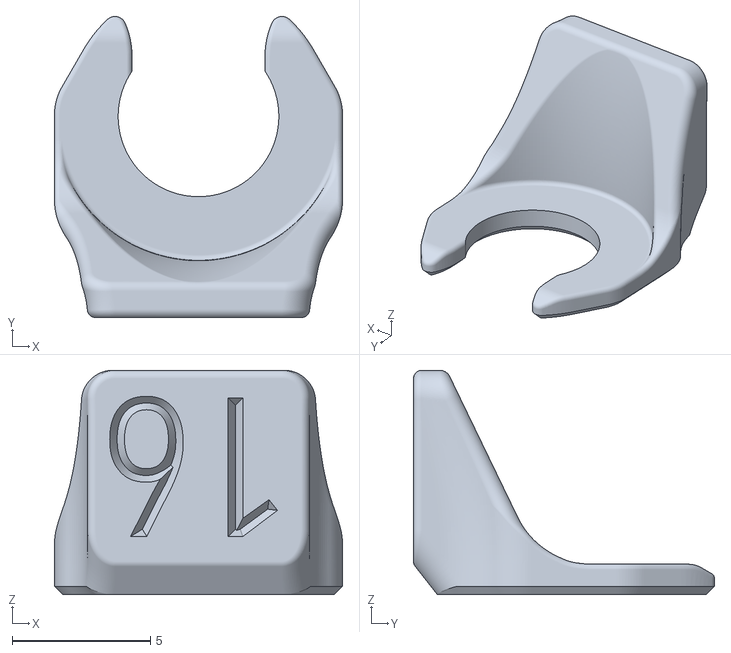
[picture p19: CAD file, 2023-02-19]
STLs/Stationary Parts/Numbered Collet Clips/number_16_collet_clip_x1_rev1.STL
10.4 x 10.9 x 8.10

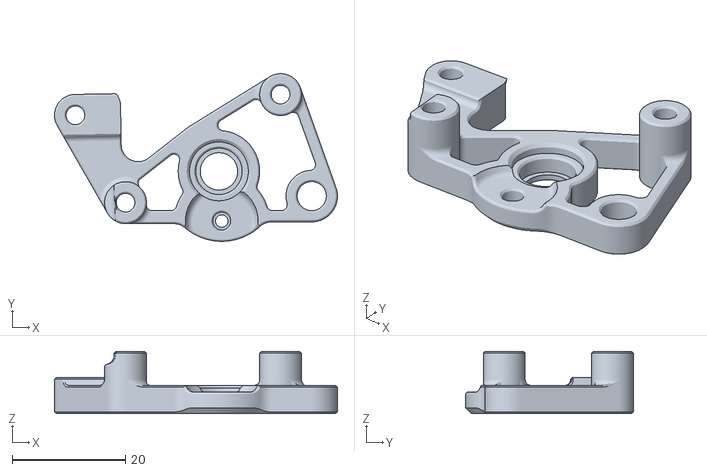
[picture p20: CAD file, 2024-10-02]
STLs/Tilting Extruder Driver/gear_casing_right_x1_rev6.STL
50.0 x 29.6 x 11.0

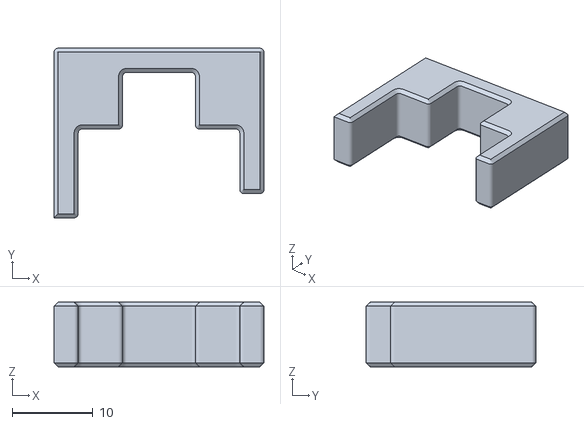
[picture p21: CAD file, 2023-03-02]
STLs/Tools/[a]_rail_installation_guide_x2_rev1.stl
26.0 x 21.0 x 8.00

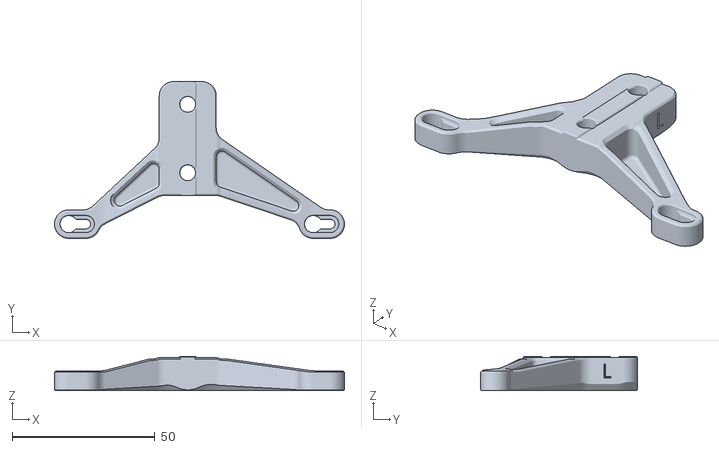
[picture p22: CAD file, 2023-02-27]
STLs/Trad Rack Mounts/K3 Side Mount/k3_side_mount_left_x1_rev3.STL
101.8 x 55.0 x 12.1

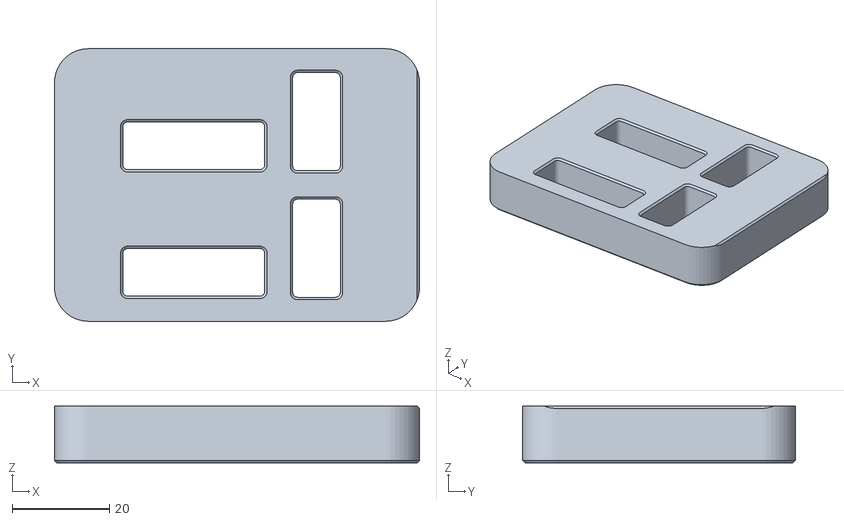
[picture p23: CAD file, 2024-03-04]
PCBs/Assembly_Jigs/tr-lower-carabiner-distribution-board-flat.STL
75.0 x 56.0 x 11.7

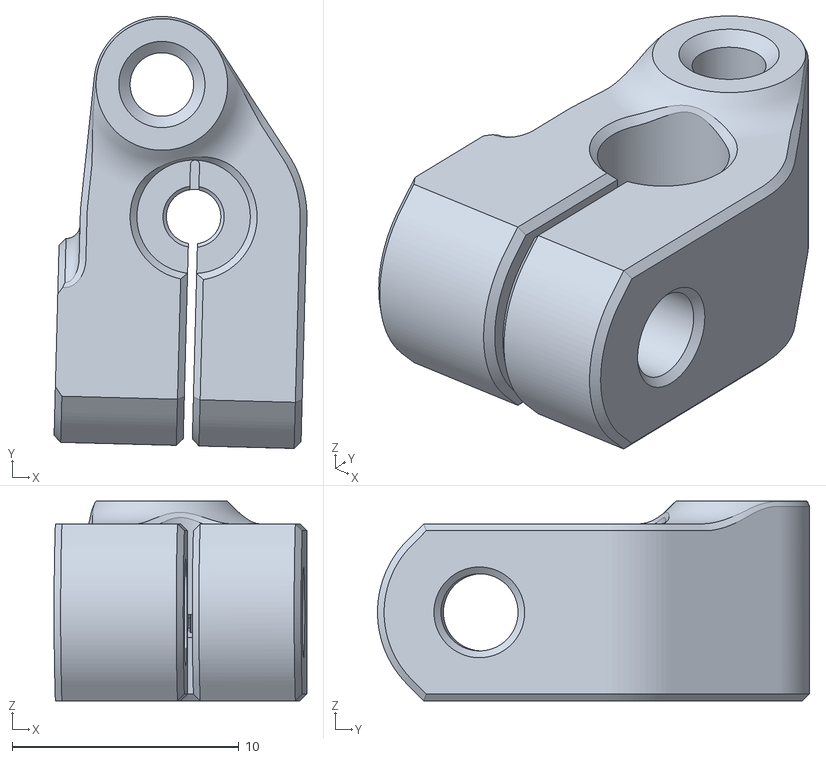
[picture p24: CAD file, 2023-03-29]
STLs/Experimental/9g servo parts/servo_horn_(9g_servo)_x1_rev2.STL
11.2 x 19.1 x 8.80

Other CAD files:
STLs/Selector/servo_horn_x1_rev2.STL
STLs/Stationary Parts/[a]_rail_stop_mgn9_x1_rev2.STL
STLs/Stationary Parts/Numbered Collet Clips/number_18_collet_clip_x1_rev1.STL
STLs/Tilting Extruder Driver/gear_casing_left_x1_rev6.STL
PCBs/Assembly_Jigs/tr-toolhead-board-flat-1.STL
PCBs/Assembly_Jigs/tr-toolhead-board-flat-2.STL
STLs/Stationary Parts/Numbered Collet Clips/[a]_number_0_collet_clip_x1_rev1.STL
STLs/Stationary Parts/Numbered Collet Clips/[a]_number_10_collet_clip_x1_rev1.STL
STLs/Stationary Parts/Numbered Collet Clips/[a]_number_15_collet_clip_x1_rev1.STL
STLs/Stationary Parts/Numbered Collet Clips/[a]_number_5_collet_clip_x1_rev1.STL
STLs/Stationary Parts/Numbered Collet Clips/number_11_collet_clip_x1_rev1.STL
STLs/Stationary Parts/Numbered Collet Clips/number_12_collet_clip_x1_rev1.STL
STLs/Stationary Parts/Numbered Collet Clips/number_13_collet_clip_x1_rev1.STL
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

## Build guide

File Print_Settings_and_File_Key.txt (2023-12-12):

Primary Color: nothing at start of file name
Accent Color: [a]_ at start of file name
Quantity Required: _x# near end of file name
File Revision: _rev# at end of file name

Do not use XY compensation, hole shrinking compensation, or any
similar slicer setting that modifies the geometry to try to account
for shrinkage. Elephant foot compensation (also known as XY first
layer compensation) is okay.

Nozzle Size: 0.5mm 
Recommended FDM Materials: ASA, Polymaker or 3DXTech Recommended
Alternate Approved FDM Materials: PC, 3DXTech Recommended
Layer Height: 0.20mm to 0.25mm
Extrusion Width: Forced 0.5mm
Infill Percentage: 40% minimum (at 0.8mm Width)
Infill Type: Grid, Gyroid, Honeycomb, Triangle or Cubic
Wall Count: 3 minimum (at 0.5mm Width)
Solid Top/Bottom Layers: 4 minimum (at 0.5mm Height)

Nozzle Size: 0.4mm 
Recommended FDM Materials: ASA, Polymaker or 3DXTech Recommended
Alternate Approved FDM Materials: PC, 3DXTech Recommended
Layer Height: 0.20mm to 0.25mm
Extrusion Width: 0.40 to 0.45mm
Infill Percentage: 40% minimum (at 0.6mm Width)
Infill Type: Grid, Gyroid, Honeycomb, Triangle or Cubic
Wall Count: 4 minimum (at 0.4mm Width)
Solid Top/Bottom Layers: 4 minimum (at 0.25mm Height)

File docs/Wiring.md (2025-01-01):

# Wiring

This document provides information on wiring for Trad Rack.

**Table of Contents**
- [Control board connections](#control-board-connections)
- [Selector](#selector)
  - [Selector harness](#selector-harness)
  - [Servo cable](#servo-cable)
  - [Stepper cable](#stepper-cable)
  - [Filament sensor cable](#filament-sensor-cable)
- [Selector stepper and endstop](#selector-stepper-and-endstop)

## Control board connections

The [selector harness](#selector-harness) and the
[selector stepper and endstop](#selector-stepper-and-endstop) will
need to be connected to the control board. This document does not
cover connections to your control board since they will depend on the
specific board you are using. If you are using
[one of the provided base config files](/Kalico/kalico_config/base_config_options/),
see the comments in the file for which pin/port to use for each
signal. Check the manufacturer's documentation if you need help
figuring out where each pin/port is located on the board.

It is recommended that you take into account your control board's
location when cutting the cables for the selector harness and the
selector stepper and endstop, but that you connect these cables to the
control board after completing all the sections in this document.

## Selector

This section covers wiring for Trad Rack's selector:

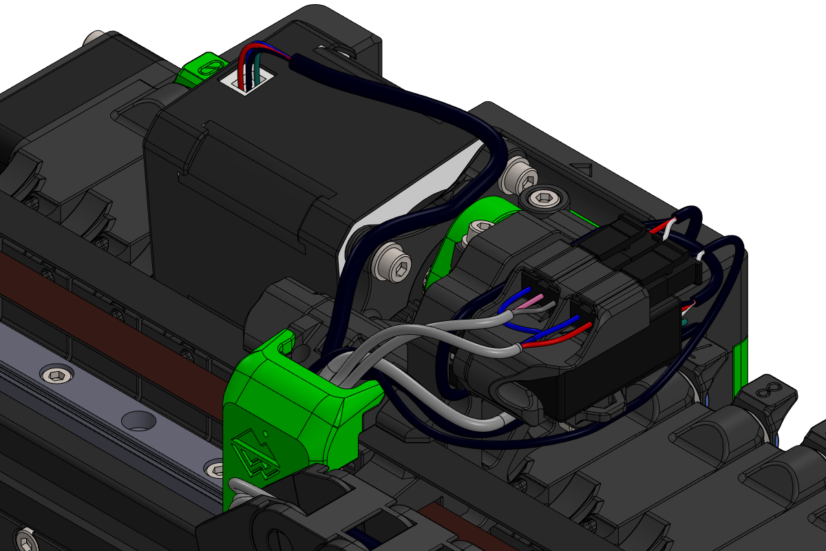
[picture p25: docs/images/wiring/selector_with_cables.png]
Selector with cables


### Selector harness

The selector harness goes from the control board, through the drag
chain, and into the Microfit holder printed part on the selector. The
Microfit plugs should be inserted into the front of the Microfit
holder and will click into place. The harness should be zip-tied to
the right carriage printed part at the location marked in red.

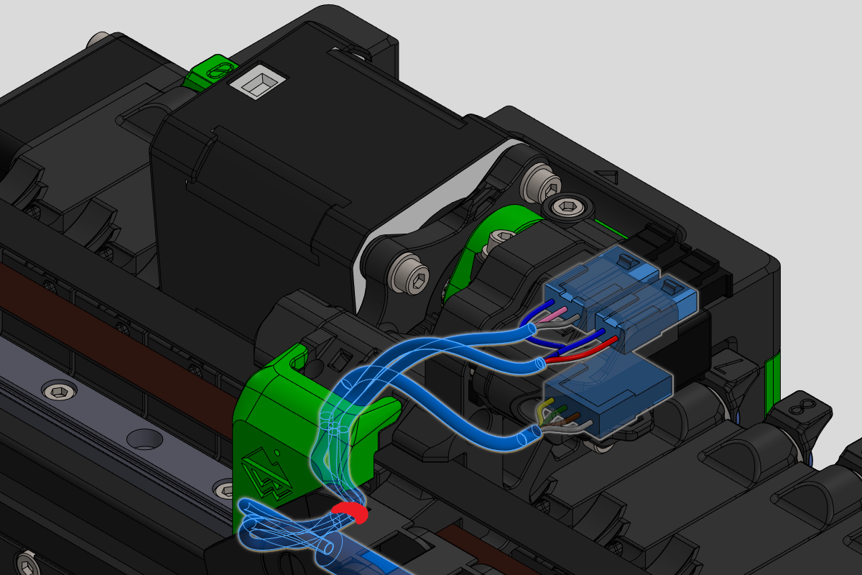
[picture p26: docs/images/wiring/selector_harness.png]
Selector harness


The length of cable between each plug and the near drag chain end
should be about 120-140mm.[^1] The overall length of the cable will
also depend on the length of your drag chain and the distance between
the fixed end of the drag chain and your control board.

[^1]: It is recommended to do a test fit before cutting any wires.

If you are using an 8-conductor cable, you will need to split the GND
wire into 2 separate wires to go into both the 3-pin Microfit plug and
the 2-pin one. This can be done by splicing wires together with a
solder joint. Wiring info is shown below:

| Wire | Color | From | From pin  | To | To pin |
| --- | --- | --- | --- | --- | --- |
| Motor A | White | Drag chain cable  | 1 | 4-pin Microfit plug | 1 |
| Motor C | Brown | Drag chain cable  | 2 | 4-pin Microfit plug | 2 |
| Motor B | Green | Drag chain cable  | 3 | 4-pin Microfit plug | 3 |
| Motor D | Yellow | Drag chain cable  | 4 | 4-pin Microfit plug | 4 |
| Servo signal | Gray | Drag chain cable  | 5 | 3-pin Microfit plug | 3 |
| 5V | Pink | Drag chain cable  | 6 | 3-pin Microfit plug | 2 |
| GND | Blue | Drag chain cable  | 7 | 3-pin, 2-pin Microfit plugs | 1, 1 |
| Filament sensor signal | Red | Drag chain cable  | 8 | 2-pin Microfit plug | 2 |

### Servo cable

The servo cable goes from the servo to the matching plug in the
Microfit holder. You will need to cut the existing cable to length and
attach a 3-pin Microfit receptacle.

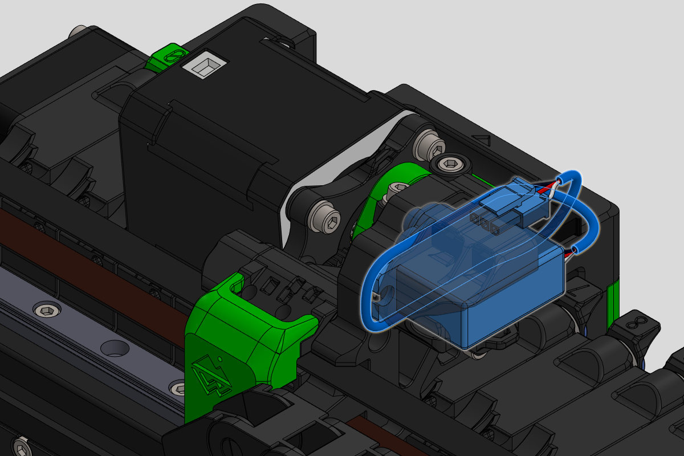
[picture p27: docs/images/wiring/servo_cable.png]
Servo cable


It is recommended to loop the servo cable around the servo as shown
above to leave some extra length in case of future changes. The length
of the cable should be about 170mm.[^1] Wiring info is shown below:

| Wire | Color | From  | From pin  | To | To pin |
| --- | --- | --- | --- | --- | --- |
| GND | Black | Servo | N/A | 3-pin Microfit receptacle | 1 |
| 5V | Red | Servo | N/A | 3-pin Microfit receptacle | 2 |
| Servo signal  | White | Servo | N/A | 3-pin Microfit receptacle | 3 |

### Stepper cable

The stepper cable goes from the filament driver stepper motor to the
matching plug in the Microfit holder. You will need to cut the
existing cable to length and attach a 4-pin Microfit receptacle.

The cable should be zip-tied to the motor plate and middle carriage
printed parts at the locations marked in red. Make sure there is
enough slack between these two ziptie points so that the cable is not
stretched when the motor pivots to lower the drive gear.

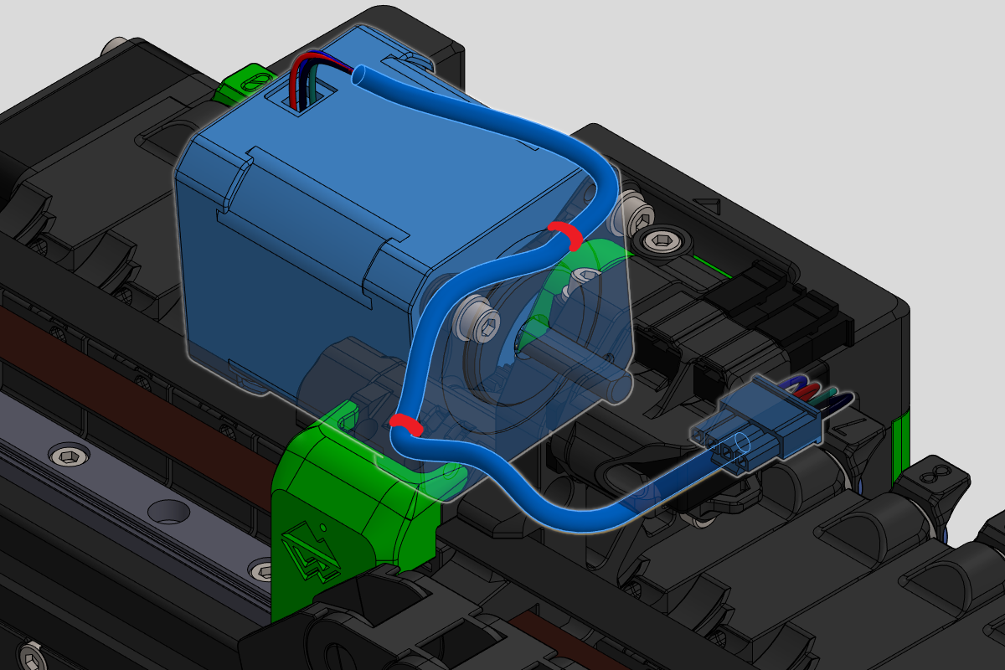
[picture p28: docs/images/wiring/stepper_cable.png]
Stepper cable


The length of the cable should be about 210mm.[^1] Wiring info is
shown below:

| Wire | Color | From | From pin  | To | To pin |
| --- | --- | --- | --- | --- | --- |
| Motor A | Black | Stepper | N/A[^2] | 4-pin Microfit receptacle | 1 |
| Motor C | Green | Stepper | N/A[^2] | 4-pin Microfit receptacle | 2 |
| Motor B | Red | Stepper | N/A[^2] | 4-pin Microfit receptacle | 3 |
| Motor D | Blue  | Stepper | N/A[^2] | 4-pin Microfit receptacle | 4 |

[^2]: If your stepper has a detachable cable and you do not already
have a premade cable that matches the colors in this table, refer to
the stepper's datasheet for which pin on the stepper's connector
corresponds to which wire/coil. The wires `Motor A` and `Motor C`
connect to one coil, and `Motor B` and `Motor D` connect to the other.

### Filament sensor cable

The filament sensor cable goes from the filament sensor microswitch
to the matching plug in the Microfit holder. To make the cable, solder
2 wires to the outer pins of the microswitch and attach the other ends
of the wires to a 2-pin Microfit receptacle. The cable should be
zip-tied to the Microfit holder at the location marked in red.

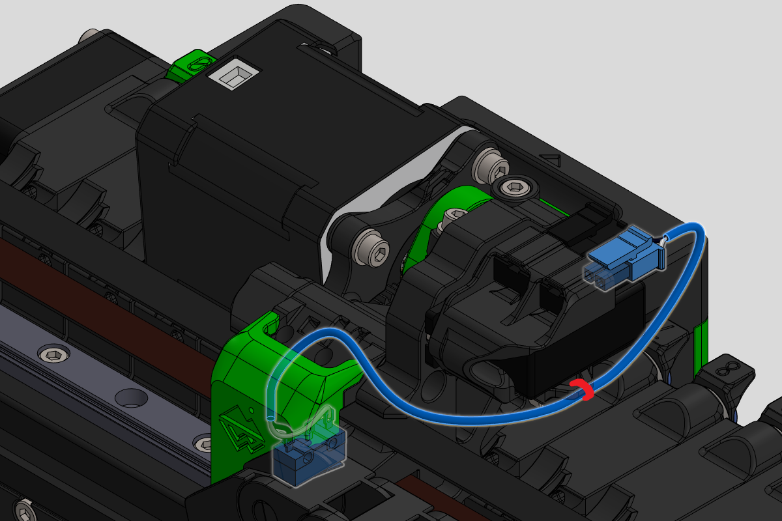
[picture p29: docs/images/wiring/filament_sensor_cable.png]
Filament sensor cable


The length of the cable should be about 155mm.[^1] Wiring info is
shown below. It does not matter which of the 2 wires goes to which
pin in the Microfit receptacle:

| Wire | Color | From | From pin  | To | To pin |
| --- | --- | --- | --- | --- | --- |
| GND | Black | D2F-L microswitch | COM | 2-pin Microfit receptacle | 1 |
| Filament sensor signal | White | D2F-L microswitch | NC | 2-pin Microfit receptacle | 2 |

## Selector stepper and endstop

The selector endstop cable goes from the endstop microswitch to the
control board. To make the cable, solder 2 wires to the outer pins of
the microswitch (and terminate the opposite ends of the wires as
necessary to connect to your control board).

The stepper cable goes from the selector stepper motor to the
control board.

The cables should be zip-tied to the lower motor mount printed part
at the locations marked in red.

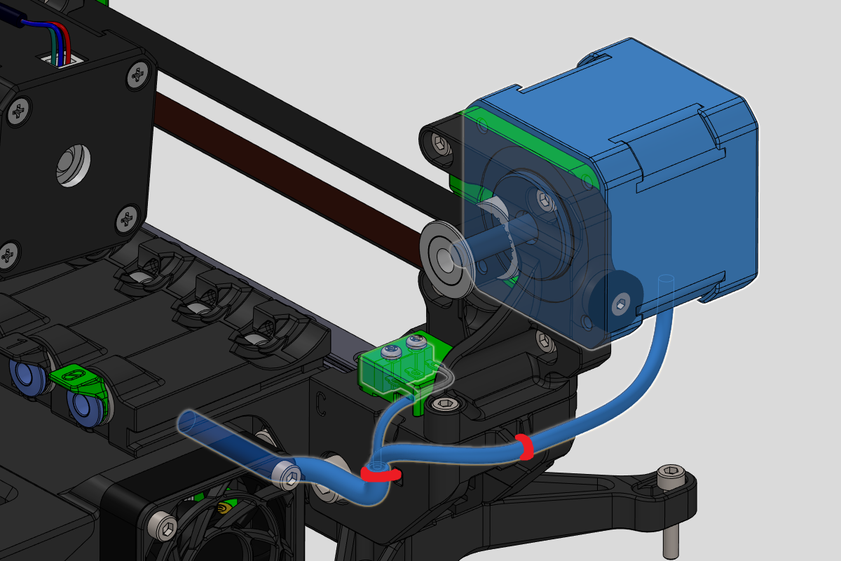
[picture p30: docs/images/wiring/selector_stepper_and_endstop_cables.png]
Selector stepper and endstop cables


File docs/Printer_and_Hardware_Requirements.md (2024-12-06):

# Printer and Hardware Requirements

This document covers prerequisites for your printer to work with Trad
Rack, as well as other hardware you might need/want to use with Trad
Rack.

**Table of Contents**
- [Printer](#printer)
- [Electronics](#electronics)
- [Toolhead filament sensor](#toolhead-filament-sensor)
- [Buffers](#buffers)
- [Mounting](#mounting)
  - [Provided mounts](#provided-mounts)
  - [Other recommended mounts](#other-recommended-mounts)
  - [Designing your own mounts](#designing-your-own-mounts)
- [Optional add-ons](#optional-add-ons)
  - [Belay (extruder sync sensor)](#belay-extruder-sync-sensor)
  - [Toolhead filament cutter](#toolhead-filament-cutter)
  - [Nozzle wiper and purge bucket](#nozzle-wiper-and-purge-bucket)

## Printer

Your 3D printer must meet the following requirements to work with Trad
Rack:

- Must use 1.75mm filament.
- Must run [Kalico](http://github.com/KalicoCrew/kalico) or
  [Klipper](https://github.com/Klipper3d/klipper) firmware.[^1]
- The toolhead or extruder must have a collet/coupling to secure a 4mm
  bowden tube at the inlet.[^2]
  
[^1]: We only provide software for using Trad Rack with Kalico or
Klipper. However, Trad Rack's hardware is not inherently reliant on
these firmwares, so you can use it with another 3D printer firmware
if you write your own software for making Trad Rack work with that
firmware.

[^2]: If you are adding a mod to your toolhead in order to add a
filament sensor, it is likely that the mod also includes support for a
bowden collet/coupling. See the table in the
[toolhead filament sensor section](#toolhead-filament-sensor) for
example recommended sensors.

## Electronics

Trad Rack requires the following ports for its actuators and sensors:

| Port | Quantity  |
| --- | --- |
| Stepper motor output port | 2 |
| Endstop input port (pins: GND, signal) | 2 |
| Servo output port (pins: GND, 5V, PWM) | 1 |

If your printer's main control board already has these ports/pins
available, you can connect Trad Rack's actuators and sensors directly
to the board. If you do not have these ports available, you may need
to use a separate control board for Trad Rack. The option of using a
separate control board attached to Trad Rack also allows you to easily
connect/disconnect Trad Rack from the rest of your printer with only
USB and power cables.

**In addition to the ports listed above, you will need a port for a
toolhead filament sensor.**[^3] This will likely be a simple endstop
input port, but it may depend on the type of sensor you use. It is
recommended to use a port either on your printer's main control board
or on a toolhead board (rather than on a separate control board
attached to Trad Rack) as doing so will likely simplify the wiring.

[^3]: A toolhead filament sensor is highly recommended for
reliability and precise filament positioning, but it is not quite
mandatory.

If you choose to use a separate control board attached to Trad Rack,
see the table below for some example recommended control board
mounts[^4]:

[^4]: If there are other control board mounts, toolhead filament
sensors, buffers, or Trad Rack mounts that you think should be added
to the tables in this document, feel free to submit pull requests to
add them. Please only submit a pull request once you have tested the
design with Trad Rack and confirmed that it works well for you.

| Board | Name/link | Comments  |
| --- | --- | --- |
| Annex Nebula  | [(provided enclosure)][1.1] | |
| BTT SKR Pico  | [Skr Pico mount for Annex tradrack][1.2] | |
| BTT SKR Pico  | [Ender 3 SKR Pico Mount (for Voron Switchwire Conversion)][1.3] | |
| Fysetc R4 | [Fysetc R4 board case mount][1.4] | |
| EASY BRD | [ERCF EasyBrd/CAN Brd mount for TR][1.5] | |

[1.1]: /STLs/Electronics%20Mounts/Nebula%20Enclosure/
[1.2]: https://github.com/v6cl/MyDIYthings/tree/main/3Dprinters/AnnexEngineeringMOD/Tradrack/PicoMount
[1.3]: https://www.printables.com/model/244991-ender-3-skr-pico-mount-for-voron-switchwire-conver
[1.4]: https://www.printables.com/model/457707-fysetc-r4-board-case-mount/files
[1.5]: https://www.printables.com/model/481199-ercf-easybrdcan-brd-mount-for-tr

## Toolhead filament sensor

Using a filament sensor on your printer's toolhead is highly
recommended.[^3] This sensor can have its trigger point be above the
extruder gears, below the extruder gears, or at the extruder gears
(e.g. by sensing the idler arm movement). See the table below for
some example recommended sensors[^4]:

| Designed for (printer/toolhead/extruder)  | Name/link | Trigger location | Comments  |
| --- | --- | --- | --- |
| All	 | [Inline Filament Sensor][2.1] | Above extruder gears  | Meant as a universal fallback option if you can't find a sensor designed for your setup. Requires that the toolhead/extruder has a bowden coupling/collet.  |
| Sherpa Mini	 | [Sherpa Mini Idler Filament Sensor and Collet][2.2] |	At extruder gears | |
| Sherpa Mini | [Sherpa Mini extruder filament sensor and Collet Mod][2.3] | Above extruder gears  | |
| Sherpa Micro	 | [Sherpa Micro Idler Filament Sensor and Collet][2.4] | At extruder gears | |
| Sherpa Micro | [Sherpa Micro extruder filament sensor and Collet Mod][2.5] | Above extruder gears  | |
| Clockwork 2 (Voron Stealthburner)	 | [CW2 with sensor, magnet, and ECAS][2.6]		 | Below extruder gears  | |
| EVA 3	 | [EVA 3 Toolhead Filament Sensor (Mechanical and Reliable)][2.7] |	Below extruder gears  | |
| E34M1	 | [E34M1 Toolhead Filament Sensor][2.8]		 | Below extruder gears  | |

[2.1]: https://github.com/Annex-Engineering/Annex-Engineering_User_Mods/tree/main/Printers/All_Printers/Ryan_G-Inline_Filament_Sensor
[2.2]: https://github.com/Annex-Engineering/Annex-Engineering_User_Mods/tree/main/Extruders/Sherpa_Mini/Extruder_Mods/Ryan_G-Idler_Filament_Sensor_and_Collet
[2.3]: https://github.com/v6cl/MyDIYthings/tree/main/3Dprinters/AnnexEngineeringMOD/SherpaMini/SherpaMiniFilamentSensor
[2.4]: https://github.com/Annex-Engineering/Annex-Engineering_User_Mods/tree/main/Extruders/Sherpa_Micro/Extruder_Mods/Ryan_G-Idler_Filament_Sensor_and_Collet
[2.5]: https://github.com/v6cl/MyDIYthings/tree/main/3Dprinters/AnnexEngineeringMOD/SherpaMicro/SherpaMicroFilamentSensor
[2.6]: https://www.printables.com/model/530705-cw2-with-sensor-magnet-and-ecas
[2.7]: https://www.printables.com/model/442650-eva-3-toolhead-filament-sensor-mechanical-and-reli
[2.8]: https://www.printables.com/model/655548-e34m1-toolhead-filament-sensor

## Buffers

Trad Rack requires a buffer for each filament.[^5] The buffer provides
a place for filament to collect when it is retracted from the toolhead
back into Trad Rack, while ensuring that the filament does not get
tangled when it needs to be used again.

[^5]: It is also possible to use an "air buffer": a short section of
bowden tube is attached to the spool holder and another to Trad Rack's
lane module, and a gap is allowed to form between the 2 tubes for the
filament to expand. This setup is not recommended as a permanent
solution since it is very messy and the filaments may tangle with each
other. However, if the filaments are separated from each other so that
they cannot tangle, this setup can be very reliable.

The following are some items you may want to take into consideration
when selecting a buffer design:

- Filament capacity: each buffer must be able to fit a length of
  filament approximately equal to the length of the bowden tube
  between Trad Rack and the printer's toolhead/extruder.
- Number of filament loops: some buffer designs wrap the filament
  around a wheel. The filament can be looped around the wheel for part of a
  revolution, a full revolution, or multiple revolutions. In general, a buffer
  with more loops takes up less space for the same filament capacity, while a
  buffer with less loops does not add as much resistance to filament movement.
  If you have the space for it, a buffer with 1 or less loops is preferred.
- Snag points and filament constraint: some buffer designs with wheels
  may have the possibility for filament to slip around the wheel and
  get stuck. It is important to keep the filament well-constrained and
  prevent snagging. In addition, it is important to ensure the filament does not
  cross over itself in ways that may cause a tangle.
- Induced filament movement: it is important that the buffer does not
  push or pull the filament while it is buffered, as this may block
  the movement of Trad Rack's selector or prevent Trad Rack from being
  able to grab the filament. Long narrow buffers (in which the filament follows
  one wall, makes a U-turn, and follows an opposite parallel wall back) are
  particularly good at avoiding this problem, since the only forces exerted by
  the walls of the buffer on the filament are perpendicular to the filament. If
  you are having problems with the buffer causing the filament to move, you can
  try adding a section of PTFE tube with a 2mm inner diameter at the inlet to
  Trad Rack's filament modules to add more resistance. See the
  [Extruder Syncing document](Extruder_Syncing.md) for ways to compensate for
  the added resistance by using Trad Rack as a secondary extruder.
- Bend radius: different filament types may require a different minimum bend
  radius in order to avoid breaking the filament or causing excess resistance in
  the filament path. For example, filled filaments may require a larger minimum
  bend radius than non-filled filaments. It is important to select a buffer that
  satisfies the largest minimum bend radius of the filaments you might use.
- Mounting: some buffer designs are meant to be attached to the
  printer. Others fit inside a filament drybox so that the filament
  inside the buffer is kept dry. You may want to consider how the
  buffer will fit into your printer and filament management setup when
  selecting a buffer design.

See the table below for some example recommended buffers[^4]:

| Filament capacity | Name/link | Comments  |
| --- | --- | --- |
| 3 sizes: 640mm, 1068mm, or 1294mm | [Stern-Wheeler][3.1] | |
| 900mm |	[MMU Filament Buffer ~900mm][3.2] |	 |
| 550mm	 | [Bigger 6 Bay Slot Buffer][3.3] |	 |
| depends on acrylic/cardboard length |	[Simple Slot Buffer][3.4]	 | |
| 300-1800mm (see table in readme)	  | [piKa][3.5]	 | |

[3.1]: https://www.printables.com/model/472316-stern-wheeler
[3.2]: https://www.printables.com/model/377512-mmu-filament-buffer-900mm
[3.3]: https://www.printables.com/model/381882-bigger-6-bay-slot-buffer
[3.4]: https://www.printables.com/model/672453-simple-slot-buffer
[3.5]: https://github.com/geoffrey-young/pika-filament-buffer

## Mounting

Trad Rack can be mounted however you want: to your printer, to a
filament storage enclosure, to a table, etc. For most setups, it will
likely be most convenient to mount Trad Rack directly to your printer.

### Provided mounts

We provide mounting brackets for attaching Trad Rack to the side of an
Annex K3 printer; these brackets can be found in the
[Trad Rack Mounts folder](/STLs/Trad%20Rack%20Mounts/).

### Other recommended mounts

The following community-designed mounts are also recommended[^4]:

| Designed for | Name/link | Comments |
| --- | --- | --- |
| Voron Trident/V2.4  |	[Offset 2020 mount for Voron's][4.1] | Requires an extra-long extrusion  |
| Voron Trident/V2.4	| [BYOLE teookie's Offset 2020 mount for Vorons][4.2] | Requires an extra-long extrusion  |
| Voron Trident/V2.4  | [Tradrack "beta" 45 angle mount voron][4.3] |	Requires K3 side mount brackets as well. May require an extra-long extrusion. |

[4.1]: https://www.printables.com/model/530709-offset-2020-mount-for-vorons
[4.2]: https://www.printables.com/model/647797-teookies-byole-offset-2020-mount-for-vorons
[4.3]: https://www.printables.com/model/462561-tradrack-beta-45-angle-mount-voron

### Designing your own mounts

The recommended way to mount Trad Rack is to attach brackets to the
underside of its 2020 extrusion, and then attach those brackets to
whatever you are mounting Trad Rack to. Depending on your setup, you
may also want to consider using an extra-long extrusion for Trad Rack
so that you can use more sides of the extrusion to attach brackets at
the ends.

It is recommended that the underside of Trad Rack's extrusion is
spaced at least 11.6mm from any surface below it in order to maintain
compatibility with any electronics mounts that are attached to the
underside of the extrusion.

## Optional add-ons

The following are optional items that can be added to your printer for
use with Trad Rack.

### Belay (extruder sync sensor)

See the [Extruder Syncing document](Extruder_Syncing.md).

### Toolhead filament cutter

An alternative to PrusaSlicer's tip-shaping process for getting clean
filament tips at the beginning of an unload is to use a filament
cutter. A filament cutter cuts off the end of the filament, which may
be bulged or stringy, in order to leave a clean end.

Trad Rack currently supports using a filament cutter mounted to the
printer's toolhead (see the
[Customization document](kalico/Customization.md#tip-shaping) for
more details on software setup). Support for a filament cutter either
inline with the bowden tube between Trad Rack and the toolhead or
mounted to Trad Rack's selector is planned but not implemented yet.

### Nozzle wiper and purge bucket

The most common method for purging material at the end of a toolchange
with Trad Rack is to use PrusaSlicer's wipe tower. However, you may
want to consider using a purge bucket with a nozzle wiper for a
portion of the purging[^6] to reduce the size of the wipe tower and
reclaim build space.

[^6]: To completely eliminate the wipe tower, additional code would be
required to tell Kalico how much material to purge depending on the
specific filaments being unloaded and loaded. However, it is
recommended to always at least use a small wipe tower to ensure the
hotend is primed for printing (as is commonly done on toolchanger and
IDEX setups).

In addition, a nozzle wiper and purge bucket may be useful if you are
replacing PrusaSlicer's ramming procedure (which deposits material on
the wipe tower) with your own tip-shaping procedure that produces
waste material that must be collected. See the
[Customization document](kalico/Customization.md#tip-shaping) for
more details on tip-shaping options.

For the Annex K3 printer, the
[trad_rack_optional.cfg config file](/Kalico/kalico_config/trad_rack_optional.cfg)
provides the option of performing the tip-shaping process over its
purge bucket and wiping the nozzle afterwards. This option can work
with other printers as well (with their own bucket/wiper setup) if
`Go_To_Purge_Location` and `Wipe_Nozzle` macros are included, either
by copying these from a provided
[K3 config file](https://github.com/Annex-Engineering/ANNEX-Printer-Firmware/tree/main/Klipper_and_Klipper_Derivatives/K3)
or by writing your own implementation of these macros (or by
modifying/replacing trad_rack_optional.cfg). If using this option on
another printer, it is recommended that you pick a bucket/wiper that
stays at a constant height relative to the toolhead so that you do not
risk the toolhead crashing into the print when it moves to the bucket.

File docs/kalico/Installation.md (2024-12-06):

# Installation

This document lists the steps to get Trad Rack set up to work with
Kalico or Klipper.

**Table of Contents**
- [Klippy module](#klippy-module)
  - [Klippy module installation](#klippy-module-installation)
  - [Enabling Moonraker updates](#enabling-moonraker-updates)
- [Config files](#config-files)
  - [Preliminary changes](#preliminary-changes)
    - [\[idle\_timeout\]](#idle_timeout)
    - [\[save\_variables\]](#save_variables)
  - [Using provided config files](#using-provided-config-files)
  - [Modifying provided config files for a different board](#modifying-provided-config-files-for-a-different-board)
  - [Building a config from scratch](#building-a-config-from-scratch)

## Klippy module

This section involves adding the Trad Rack Klippy module(s) to Klipper
and enabling updates through Moonraker.

If you are using [Kalico](http://github.com/KalicoCrew/kalico),
you can skip to [setting up config files](#config-files) since
Kalico already includes the trad_rack module.

The installation procedure differs slightly depending on whether
you are using a recent version of Klipper or an older version from
before
[commit bafb126](https://github.com/Klipper3d/klipper/commit/bafb126abd77edd0cb2e5ae3b5d99ff83272594c).

For parts of the installation procedure that differ depending on the
version of Klipper you are using, there will be an "Old" dropdown
below the commands/text that you would use with a recent
installation. In such cases, if you are using an old version of
Klipper from before commit bafb126, use the commands/text in the
dropdown instead of what is directly above.

### Klippy module installation

Run the following commands to download and install the Klippy
module(s):

```
cd ~
curl -LJO https://raw.githubusercontent.com/Annex-Engineering/TradRack/main/Kalico/klippy_module/install.sh
chmod +x install.sh
./install.sh
```
<details>
  <summary>Old</summary>
  
  ```
  cd ~
  curl -LJO https://raw.githubusercontent.com/Annex-Engineering/TradRack/main/Kalico/klippy_module/install.sh
  chmod +x install.sh
  ./install.sh pre_toolhead_changes
  ```
</details>

Then remove the install script with the following command:

```
rm install.sh
```

Finally, restart the klipper service using the following command:

```
sudo systemctl restart klipper
```

> [!TIP]
> If you ever need to run the install script again in the future (for
> example if additional Klippy modules get added), you can do so
> without recreating the `trad_rack_klippy_module` directory using the
> following commands:
> ```
> cd ~
> ./trad_rack_klippy_module/Kalico/klippy_module/install.sh <branch_name>
> ```
> If unspecified, `branch_name` defaults to `main`.

### Enabling Moonraker updates

To enable updates of the Trad Rack Klippy module(s) through Moonraker,
add the following to your `moonraker.conf` file. This file is usually
located in `~/printer_data/config/`:

```
[update_manager trad_rack]
type: git_repo
path: ~/trad_rack_klippy_module
origin: https://github.com/Annex-Engineering/TradRack.git
primary_branch: main
managed_services: klipper
```
<details>
  <summary>Old</summary>

  ```
  [update_manager trad_rack]
  type: git_repo
  path: ~/trad_rack_klippy_module
  origin: https://github.com/Annex-Engineering/TradRack.git
  primary_branch: pre_toolhead_changes
  managed_services: klipper
  ```
</details>

Then restart the moonraker service using the following command:

```
sudo systemctl restart moonraker
```

## Config files

Complete the following changes/additions to your Kalico config:

### Preliminary changes

The following preliminary changes should be made to your existing
config file(s):

#### [idle_timeout]

It is recommended to modify the [idle_timeout] section to prevent
the printer from disabling the heaters and motors if the printer is
paused. Add the following to your config file or modify `gcode` if the
[idle_timeout] section is already there:

```ini
[idle_timeout]
# only turn off heaters and motors if the printer is not paused
gcode:
    {% if not printer.pause_resume.is_paused %}
        TURN_OFF_HEATERS
        M84
    {% endif %}
```

#### [save_variables]

The [save_variables] config section is required. See the
[Kalico Config Reference document](https://docs.kalico.gg/Config_Reference.html#save_variables)
for details on how to add this section.

### Using provided config files

Copy the following files into your Kalico config folder and
[include them](https://docs.kalico.gg/Config_Reference.html#include)
in your main printer config file:

- One of the files from the
  [base_config_options folder](/Kalico/kalico_config/base_config_options/):
  base config file. Several options are provided for different boards
  or stepper drivers. This file is required. Make sure to complete the
  following changes:
  - [mcu tr] section
    - Replace `serial` with the serial for your board.
      See Kalico's 
      [Installation document](https://docs.kalico.gg/Installation.html)
      if you need help finding this value.
  - [trad_rack] section
    - Change `toolhead_fil_sensor_pin` to match the pin you are using
    for your toolhead filament sensor.
    - Change `lane_count` to match your Trad Rack.
    - Change the following values to suit your setup. See the 
      [Tuning document](/docs/Tuning.md) for more details:
        - `bowden_length`
        - `extruder_load_length`
        - `hotend_load_length`
        - `toolhead_unload_length`
  - [stepper_tr_selector] section
    - Change `position_max` accordingly depending on your 
      `lane_count`, using the formula in the config file.
  - [tmc2209 stepper_tr_selector] or [tmc5160 stepper_tr_selector]
    section
    - Change `run_current` to match your selector motor.
  - [tmc2209 stepper_tr_fil_driver] or [tmc5160 stepper_tr_fil_driver]
    section
    - Change `run_current` to match your filament driver motor.
- [trad_rack_optional.cfg](/Kalico/kalico_config/trad_rack_optional.cfg):
  optional config file. It is highly recommended to include this file
  (see the [Customization document](Customization.md) for more
  details).

### Modifying provided config files for a different board

Follow the instructions in
[using provided config files](#using-provided-config-files). In
addition, modify every "pin" or "uart_address" setting in
the base config file to match your board: copy each of these settings
from a corresponding section in the
[example Kalico config for your board](https://github.com/KalicoCrew/kalico/tree/main/config).
Some settings such as `tx_pin` or `uart_address` might not be needed.

### Building a config from scratch

See the [Config Reference document](Config_Reference.md) for the
required configuration sections and parameters for Trad Rack.

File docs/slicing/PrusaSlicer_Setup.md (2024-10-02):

# PrusaSlicer Setup

This document explains how to add the provided PrusaSlicer profiles
to your slicer, as well as setup tips pertaining to PrusaSlicer
specifically. Setting names used here follow the "parameter names"
that are used in the slicer config files; you can use the search
function to see which settings these correspond to in the GUI.

**Table of Contents**
- [Adding provided profiles](#adding-provided-profiles)
- [Extruder count](#extruder-count)
- [Setting up a print](#setting-up-a-print)
- [Modifying the profiles](#modifying-the-profiles)
- [Experimental options](#experimental-options)

## Adding provided profiles

A vendor bundle for PrusaSlicer 2.7.0 can be found in the
[PrusaSlicer_2.7.0 folder](/Slicer_Config/PrusaSlicer_2.7.0). To use
the included profiles, first copy the contents of the folder to the
`vendor` folder located in:

- PrusaSlicer ***stable***\* version:
  - Windows: `C:\Users\<username>\AppData\Roaming\PrusaSlicer`
  - Mac: `/Users/<username>/Library/Application Support/PrusaSlicer`
- PrusaSlicer ***alpha***\* version:
  - Windows: `C:\Users\<username>\AppData\Roaming\PrusaSlicer-alpha`
  - Mac: `/Users/<username>/Library/Application Support/PrusaSlicer-alpha`
- PrusaSlicer ***beta***\* version:
  - Windows: `C:\Users\<username>\AppData\Roaming\PrusaSlicer-beta`
  - Mac: `/Users/<username>/Library/Application Support/PrusaSlicer-beta`

\* the vendor .ini file will have the slicer version it is meant for
written at the top. Make sure you check whether it is a stable, alpha,
or beta version so that you copy the items to the correct folder.

Next, launch PrusaSlicer and open the Configuration Wizard by clicking
`Configuration > Configuration Wizard`. Click on "Other Vendors" on
the left side (or "Other FFF" on PrusaSlicer 2.8 or later) and ensure
"Annex Engineering" is checked.

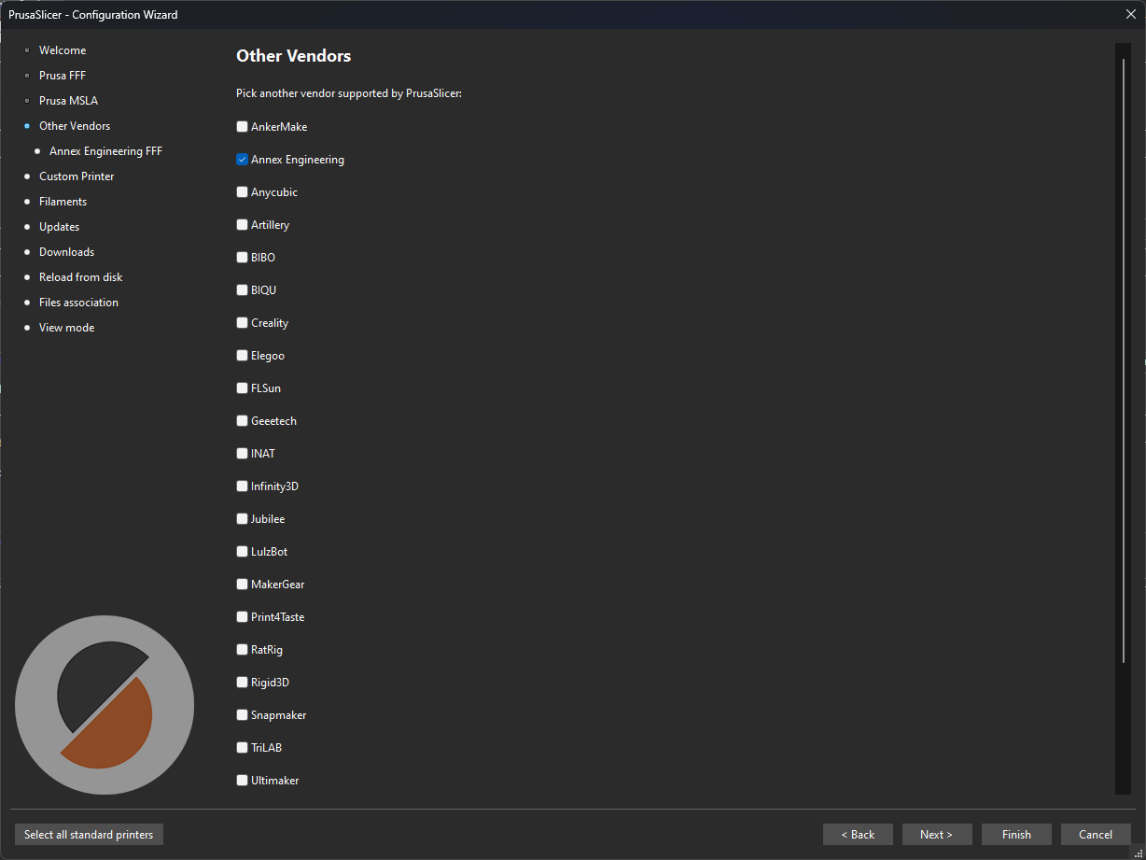
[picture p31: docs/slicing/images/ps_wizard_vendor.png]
Check "Annex Engineering"


Click on "Annex Engineering FFF" on the left and select the printer
profile(s) you want to add.

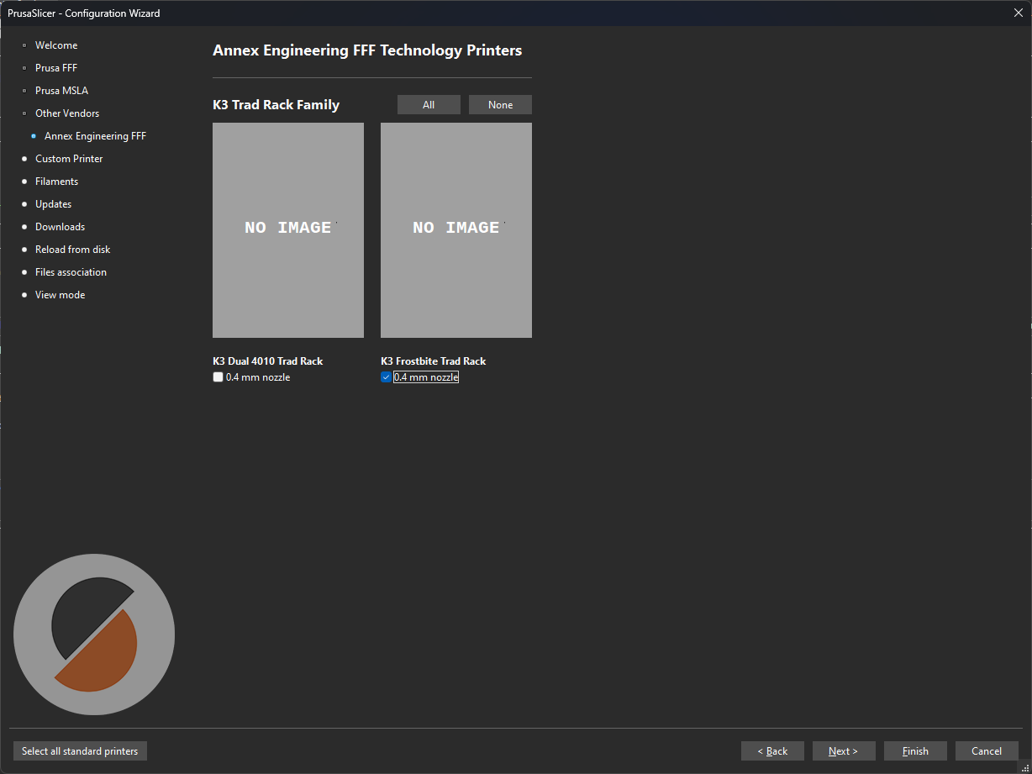
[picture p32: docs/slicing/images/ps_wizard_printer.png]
Select printer profiles


Click on "Filaments" on the left, select the names of all the printer
profiles you added, and ensure all of the filament profiles you want
are checked by clicking the "All" button on the right.

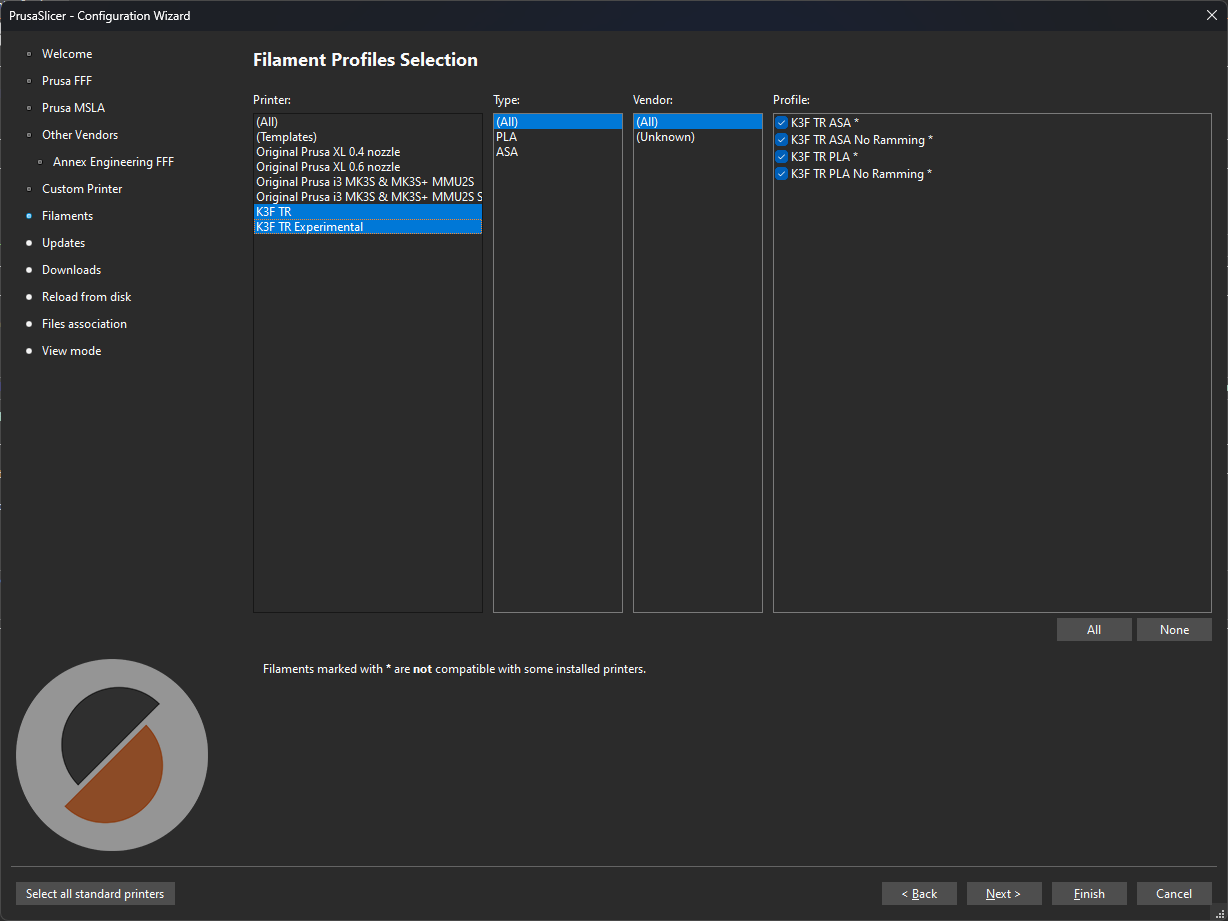
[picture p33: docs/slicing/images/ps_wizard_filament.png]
Select filament profiles


Finally, click Finish. In the Plater tab, you should now be able to
select the Printer, Print settings, and Filament from the profiles
you just added.

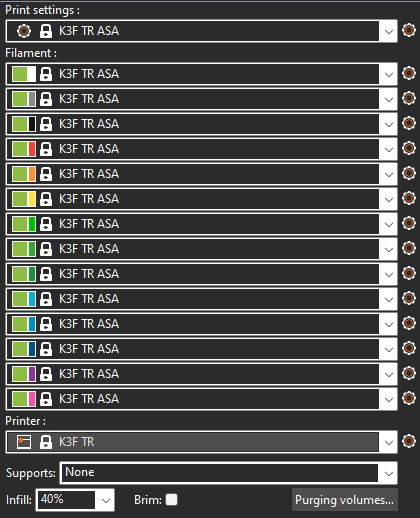
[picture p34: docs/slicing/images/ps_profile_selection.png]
Plater: select profiles


## Extruder count

Set `extruders_count` to match the number of lanes on your Trad Rack.
This setting is located in the Printer Settings Tab.

## Setting up a print

See "9 Printing in Multi Material Mode" in the 
[Prusa MMU2S manual](https://www.prusa3d.com/downloads/manual/prusa3d_manual_mmu2s_en.pdf)
for details on how to set up a multimaterial print. In particular,
make sure to set the purge volumes, as these cannot be saved in a
profile.

## Modifying the profiles

If you modify the print, filament, or printer settings in the slicer,
you can use the save button to save a copy of your settings. A .ini
file will be saved to the corresponding `print`, `filament`, or
`printer` folder, located in the same parent folder as the `vendor`
folder. Alternatively, you can edit the `Annex_K3_TR.ini` file
directly in a text editor if you prefer.

## Experimental options

See the [Slicing document](Slicing.md#experimental-options) for more
details.

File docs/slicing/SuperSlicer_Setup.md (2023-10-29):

# SuperSlicer Setup

This document explains how to add the provided SuperSlicer profiles
to your slicer, as well as setup tips pertaining to SuperSlicer
specifically. Setting names used here follow the "parameter names"
that are used in the slicer config files; you can use the search
function to see which settings these correspond to in the GUI.

**Table of Contents**
- [Adding provided profiles](#adding-provided-profiles)
- [Extruder count](#extruder-count)
- [Setting up a print](#setting-up-a-print)
- [Purge volumes](#purge-volumes)
- [Modifying the profiles](#modifying-the-profiles)
- [Experimental options](#experimental-options)

## Adding provided profiles

A vendor bundle for SuperSlicer 2.4.58 can be found in the
[SuperSlicer_2.4.58 folder](/Slicer_Config/SuperSlicer_2.4.58). To use
the included profiles, first copy the contents of the folder to the
`vendor` folder located in:

- Windows: `C:\Users\<username>\AppData\Roaming\SuperSlicer`
- Mac: `/Users/<username>/Library/Application Support/SuperSlicer`

Next, launch SuperSlicer and open the Configuration Wizard by clicking
`Configuration > Configuration Wizard`. Click on "Annex Engineering"
on the left and select the printer profile(s) you want to add.

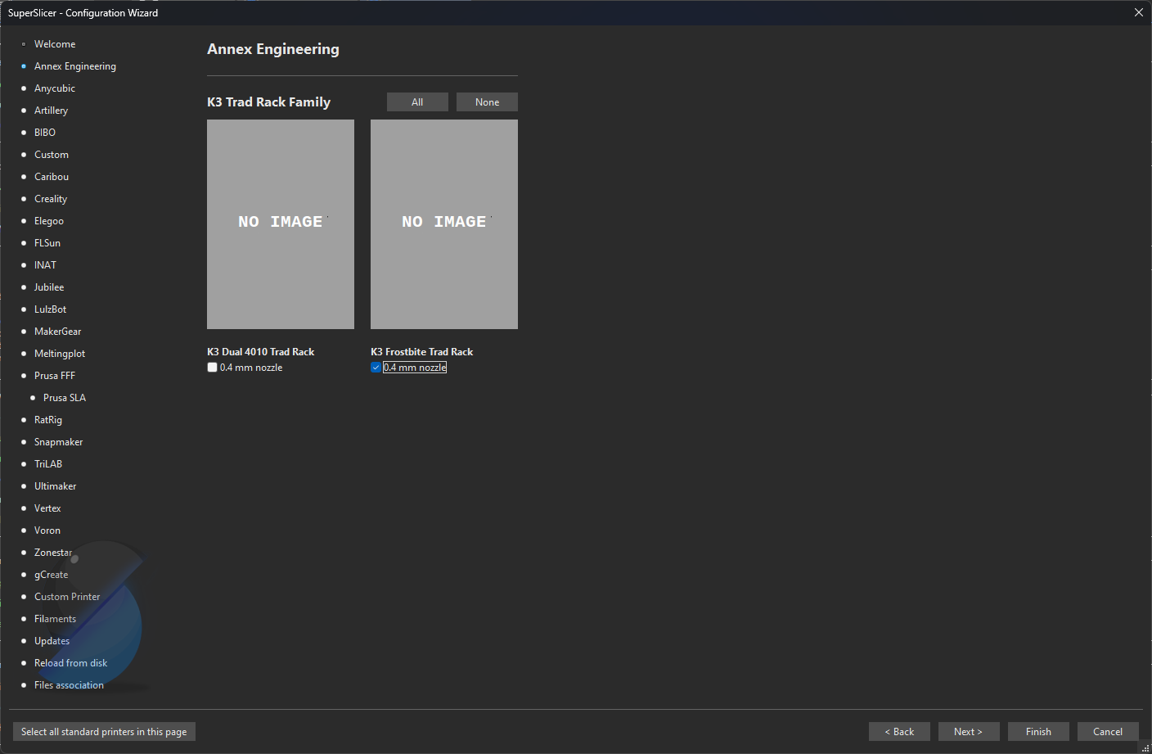
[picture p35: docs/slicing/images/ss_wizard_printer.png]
Select printer profiles


Click on "Filaments" on the left, select the names of all the printer
profiles you added, and ensure all of the filament profiles you want
are checked by clicking the "All" button on the right.

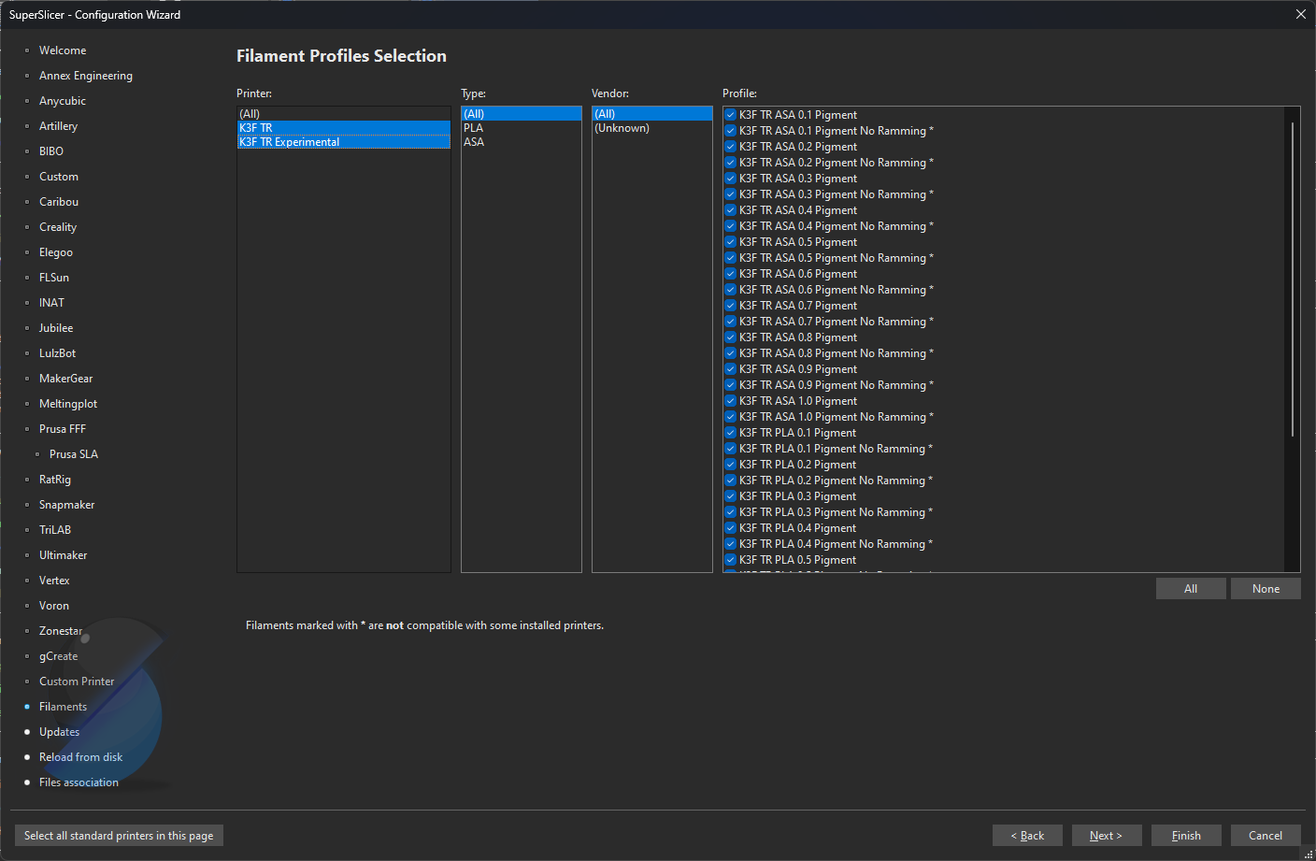
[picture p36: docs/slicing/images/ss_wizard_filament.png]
Select filament profiles


Finally, click Finish. In the Plater tab, you should now be able to
select the Printer, Print settings, and Filament from the profiles
you just added.

Plater: select profiles

## Extruder count

Set `extruders_count` to match the number of lanes on your Trad Rack.
This setting is located in the Printer Settings Tab.

## Setting up a print

See "9 Printing in Multi Material Mode" in the 
[Prusa MMU2S manual](https://www.prusa3d.com/downloads/manual/prusa3d_manual_mmu2s_en.pdf)
for details on how to set up a multimaterial print. In particular,
make sure to set the purge volumes, as these cannot be saved in a
profile.

## Purge volumes

In addition to the "Purging volumes" settings accessible from the
Plater tab, SuperSlicer has the ability to calculate purge volumes
automatically based on the pigment number assigned to each filament
(a decimal between 0 and 1). This is called "Advanced wipe tower purge
volume calculs". If this is enabled (by setting `wipe_advanced` to
true), the "Purging volumes" tables will be ignored. The provided
profiles have this enabled by default. Filament profiles with
various pigment amounts in 0.1 increments are included. If you leave
automatic purge volume calculation enabled, make sure to select the
corresponding filament profile in the Plater tab for each tool.

The purge volumes used in the provided profiles are for a mosquito
magnum, but I have not done much experimentation or optimization.
I would recommend doing your own tuning on purge volumes, try
different wipe advanced algorithms, try the purging volumes tables if
you prefer, etc. You can access the multiplier and algorithm settings,
as well as enable or disable automatic purge volume calculations, in
the "Single Extruder MM setup" section in the Printer Settings tab.
You might need to uncheck and recheck `single_extruder_multi_material`
in the Printer Settings tab to get this section to appear.

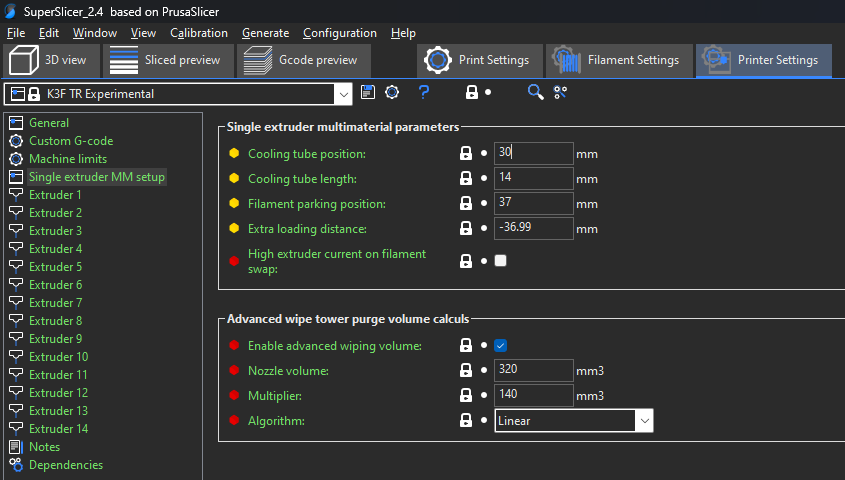
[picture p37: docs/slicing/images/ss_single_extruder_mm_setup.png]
Single extruder MM setup


## Modifying the profiles

If you modify the print, filament, or printer settings in the slicer,
you can use the save button to save a copy of your settings. A .ini
file will be saved to the corresponding `print`, `filament`, or
`printer` folder, located in the same parent folder as the `vendor`
folder. Alternatively, you can edit the `Annex_K3_TR.ini` file
directly in a text editor if you prefer.

## Experimental options

See the [Slicing document](Slicing.md#experimental-options) for more
details.

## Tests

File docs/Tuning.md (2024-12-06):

# Tuning

This document provides an overview of the loading and unloading
processes and how to tune them.

**Table of Contents**
- [Loading process](#loading-process)
- [Unloading process](#unloading-process)
- [Tuning lengths](#tuning-lengths)
  - [Bowden length](#bowden-length)
  - [Toolhead-specific lengths](#toolhead-specific-lengths)
- [Bowden lengths](#bowden-lengths)
  - [Relevant config options](#relevant-config-options)
  - [How calibration works](#how-calibration-works)
  - [Saving and restoring bowden lengths](#saving-and-restoring-bowden-lengths)
- [Bowden speeds](#bowden-speeds)

## Loading process

The following table shows the actions taken in sequential order when
loading filament from Trad Rack into the toolhead, as well as some
details about each action: distance of each move, speed of the move,
whether Trad Rack's filament driver motor is involved, and whether the
printer's main extruder is involved.

| Description | Distance (mm) | Speed (mm\s) | Trad Rack filament driver | Main extruder |
| --- | --- | --- | --- | --- |
| move through bowden tube | ["bowden_load_length"](#bowden-lengths) | see [bowden speeds](#bowden-speeds) | :white_check_mark: | :x: |
| toolhead sensor homing[^1]  | until sensor triggers[^2] | `toolhead_sense_speed` | :white_check_mark: | :white_check_mark:  |
| load extruder | `extruder_load_length` | `extruder_load_speed` | :white_check_mark: | :white_check_mark:  |
| load hotend | `hotend_load_length` | `hotend_load_speed` | :white_check_mark:[^3] | :white_check_mark:  |

[^1]: This move only occurs if `toolhead_fil_sensor_pin` is specified
and `load_with_toolhead_sensor` is True.

[^2]: The maximum length of this move is defined by
`bowden_load_homing_dist`. If the sensor is still not triggered after
Trad Rack supposedly moved the filament this distance, the load will
be halted and the print will be paused.

[^3]: The servo will start disengaging Trad Rack's drive gear 
`servo_wait_ms` before the move ends, unless `sync_to_extruder` is
True (in which case the drive gear will stay engaged).

## Unloading process

The following table shows which actions are taken when unloading
filament from the toolhead back into Trad Rack.

| Description | Distance (mm) | Speed (mm/s) | Trad Rack filament driver | Main extruder |
| --- | --- | --- | --- | --- |
| toolhead sensor homing[^4]  | until sensor is untriggered[^5] | `toolhead_sense_speed`  | :white_check_mark: | :white_check_mark:  |
| unload toolhead | `toolhead_unload_length` | `toolhead_unload_speed` | :white_check_mark: | :white_check_mark:  |
| move through bowden tube | ["bowden_unload_length"](#bowden-lengths) | `buffer_pull_speed` | :white_check_mark: | :x: |
| selector sensor homing | until sensor is untriggered | `selector_sense_speed`  | :white_check_mark: | :x: |

[^4]: This move only occurs if `toolhead_fil_sensor_pin` is specified
and `unload_with_toolhead_sensor` is True.

[^5]: The maximum length of this move is defined by
`bowden_unload_homing_dist`. If the sensor is still triggered after
Trad Rack supposedly moved the filament this distance, the unload will
be halted and the print will be paused.

## Tuning lengths

The following lengths must be tuned to match your bowden tube,
extruder, toolhead, and toolhead sensor setup. The values in the
provided config file have been tuned for an Annex K3 toolhead running
a Sherpa Micro extruder (with a sensor detecting its idler arm
movement) and a Mosquito Magnum hotend.

### Bowden length

- `bowden_length` (mm): 
  - If you are using a toolhead filament sensor
    (`toolhead_fil_sensor_pin` is specified and
    `load_with_toolhead_sensor` is True):
    - You can set this to any value that is greater than half the
      actual length of the bowden tube between Trad Rack and the
      toolhead but less than the full actual length. Knowing the
      actual length precisely is not necessary because the bowden load
      and unload lengths will be calibrated automatically (see
      [bowden lengths](#bowden-lengths) for details).
  - Else:
    - This value should be slightly smaller than the
      length of the bowden tube between Trad Rack and your toolhead.
      This length should be tuned to bring the filament tip almost all
      the way to the extruder drive gears, starting from the point where
      Trad Rack's selector filament sensor is triggered. Make sure there
      is some distance between the filament tip and the drive gears for
      safety.

### Toolhead-specific lengths

- `extruder_load_length` (mm): this length should be tuned to bring
  the filament tip from the point where the toolhead sensor is
  triggered to a point slightly above the heatbreak throat. You can
  base this length off of measurements of your toolhead from CAD. If
  you are not using a toolhead sensor, then the position of the
  filament tip after moving through the bowden tube would be your
  starting point.
- `hotend_load_length` (mm): this length is meant to bring the
  filament tip from the ending point of `extruder_load_length` to a
  point inside the meltzone so it is ready for printing. You may
  have to tune this parameter through trial and error to avoid extra
  oozing during loading or gaps in your wipe tower.
- `toolhead_unload_length` (mm): this length is meant to bring the
  filament tip from the point where the toolhead sensor is untriggered
  to a point above the extruder gears (where the extruder gears will
  not touch the filament). If your toolhead sensor is above the
  extruder gears and you are confident that the filament will not be
  touching the extruder gears at the point where it is untriggered,
  this length can be as low as 0. If you are not using a toolhead
  sensor, the starting point of this move would be wherever the
  filament is when the toolchange command gets executed.[^6]

[^6]: If following the instructions in the Slicing document, the
starting point of this move (if you are not using a toolhead sensor)
will be the top of the "cooling tube." See the Slicing document for
more details. It is also okay to leave `toolhead_unload_length` at its
default value if you are not using a toolhead sensor; the toolchange
will just take a little longer.

See the drawings below for a visualization of the toolhead-specific
lengths on toolheads with various sensor setups. Colorful labels are
length settings, and black labels in parentheses are references that
are used to determine the starting or ending points of the length
settings.

| Sensor location | Drawing |
| --- | --- |
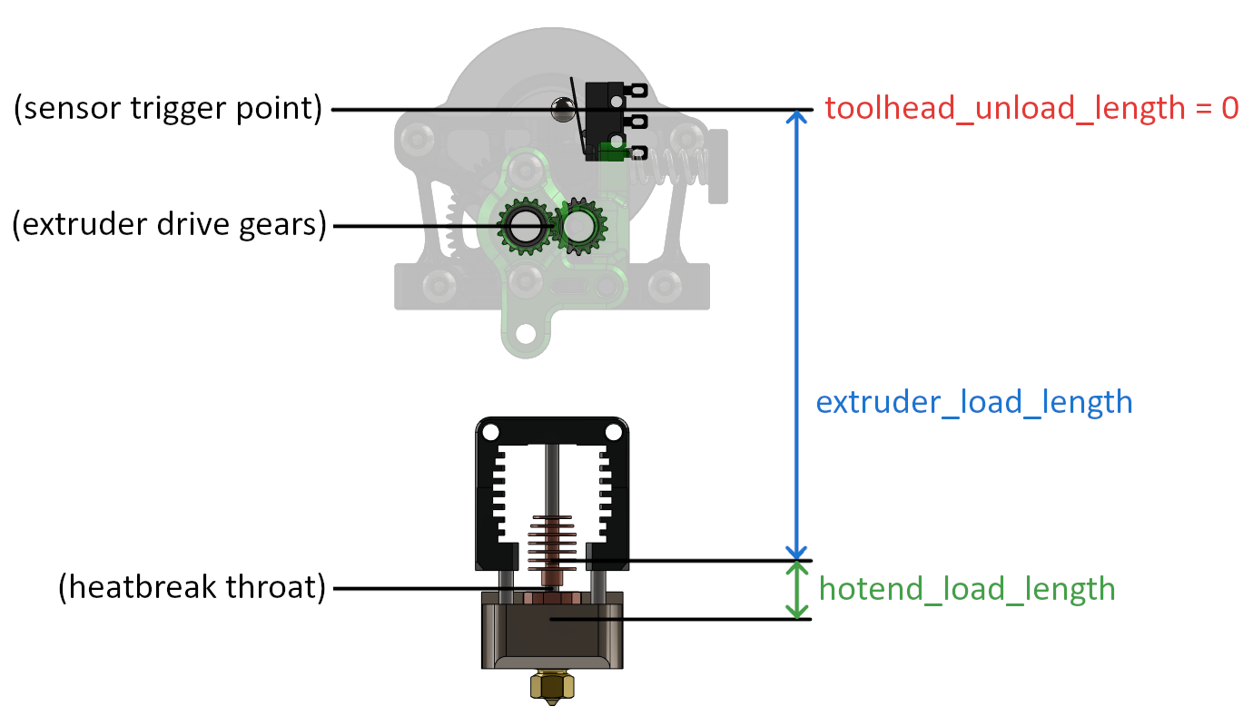
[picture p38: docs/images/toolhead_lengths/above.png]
| Sensor above extruder gears |  |
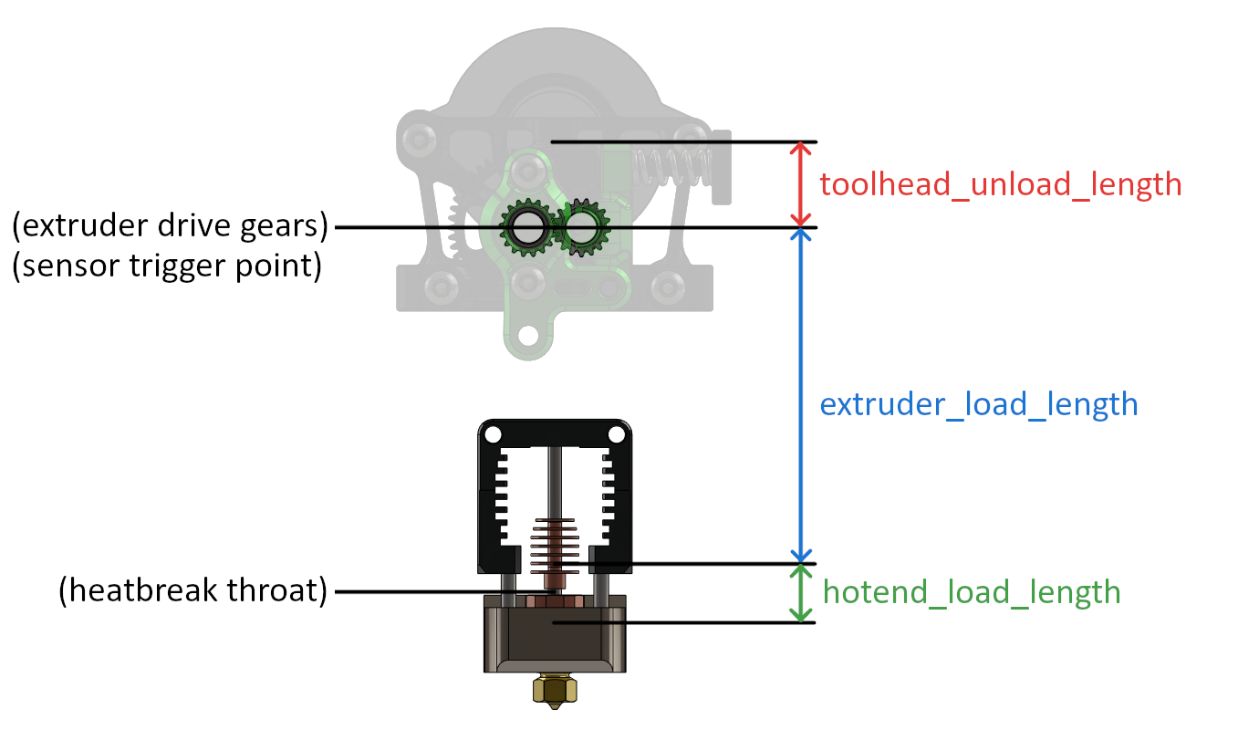
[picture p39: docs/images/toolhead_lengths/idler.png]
| Sensing idler arm movement  |  |
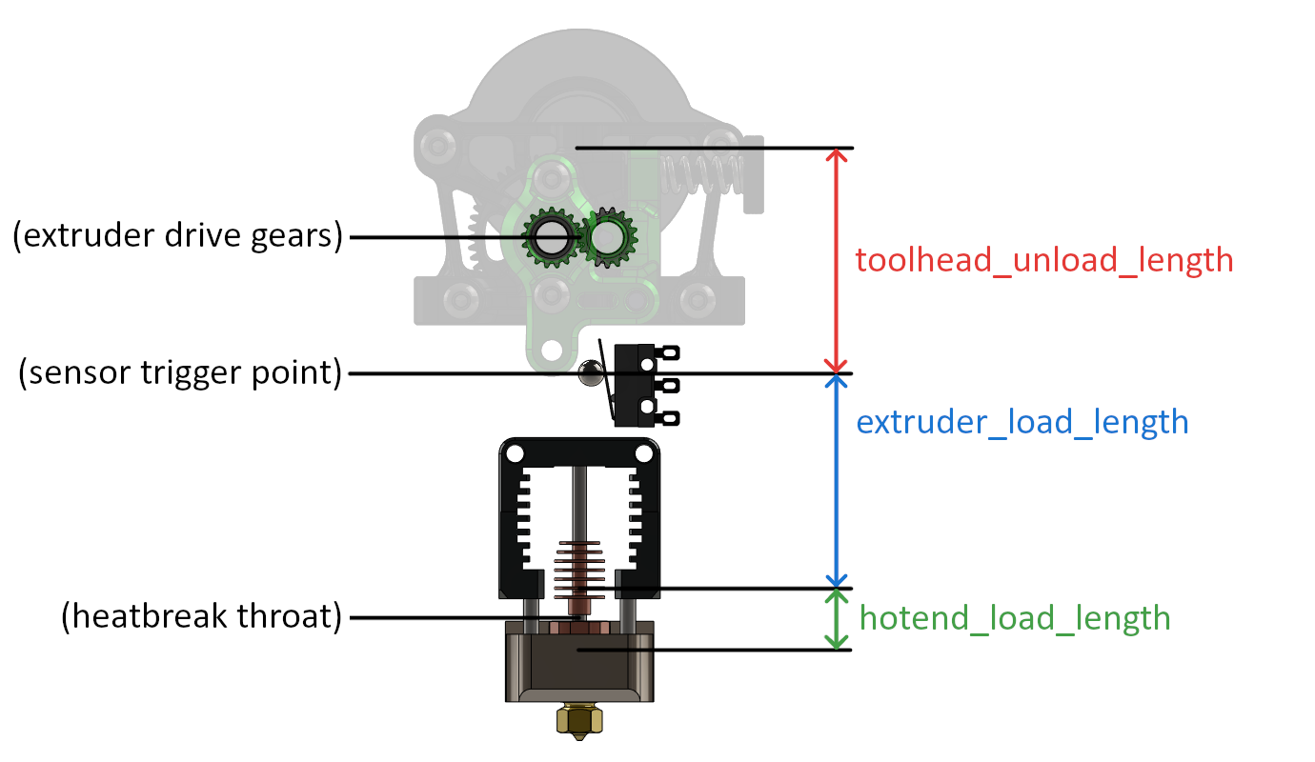
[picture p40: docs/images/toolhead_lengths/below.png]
| Sensor below extruder gears |  |

> [!NOTE]
> The bottom point of `hotend_load_length` is not drawn to scale and
> will depend on your specific hotend, tip shaping procedure, etc.

## Bowden lengths

"bowden_load_length" and "bowden_unload_length" are both initially
set to `bowden_length`, but they are each updated automatically
on every load and unload respectively.

> [!NOTE]
> If `toolhead_fil_sensor_pin` is not specified or
> `load_with_toolhead_sensor` is False, "bowden_load_length" will not be
> updated automatically and will remain equal to `bowden_length`.

### Relevant config options

The following config options are relevant to the calibration of moves
through the bowden tube. See
[how calibration works](#how-calibration-works) for an explanation of
how these values are used. It is not mandatory to set these config
options; they default to safe values but may be optimized further if
you wish:

- `fil_homing_retract_dist`
- `target_toolhead_homing_dist`
- `target_selector_homing_dist`
- `bowden_length_samples`

### How calibration works

During each sensor homing move, Trad Rack keeps track of how far its
drive gear rotates until the sensor triggers. As a result, the
distance from the start of the bowden tube move to the sensor's
trigger point can be estimated. For loading, the start of this
distance is the trigger point of the selector sensor, and the end is
the trigger point of the toolhead sensor. For unloading, the start is
the filament tip's location after the toolhead is unloaded, and the
end is the trigger point of the selector sensor.

The measured distance is the sum of the length of the fast move
through the bowden tube
and the length of the slower homing move that occurs afterwards.
`target_toolhead_homing_dist` or `target_selector_homing_dist` (for
loading or unloading respectively) is subtracted from the measured
distance to calculate a value for just the fast bowden move length.
These target distance values each represent
the target length of the slower sensor homing moves that occurs after
the fast bowden move; these slower moves should have
a nonzero length to account for any variance in the filament tip
position due to factors such as springiness or bending of the
filament. In addition, `target_toolhead_homing_dist` should be large
enough that the
fast bowden move that occurs during loading does not move the
filament far enough to hit the extruder's drive gears.
"bowden_load_length" and "bowden_unload_length" are set to try to
reach these target values.

At this point, an initial value for "bowden_load_length" or
"bowden_unload_length" has been determined based solely on the last
load or unload. A moving average is then used to determine the
value that will be set and used for the next load or unload.
`bowden_length_samples` determines the max number of measurements
that are averaged to determine this value.

The calibration process repeats on every load or unload.

In case the filament reaches the sensor early during the fast bowden
move, the move will be stopped and the filament will be retracted
away from the sensor by `fil_homing_retract_dist` (mm) before continuing
on to the slower sensor homing move. This retraction move is meant to
undo any extra displacement of the filament if the filament driver motor
skips when the fast bowden move is stopped.

### Saving and restoring bowden lengths

Bowden load and unload length data is saved to disk using
[save_variables](https://docs.kalico.gg/Config_Reference.html#save_variables)
so it can be restored across restarts. The `bowden_length` config
value is only used on the initial load and unload. However, if
`bowden_length` is set to a new value and Kalico is restarted, any
saved bowden load and unload length data will be ignored and
overwritten. Setting a new `bowden_length` allows you to discard old
saved values if you make a change to your hardware setup. See the
[Save Variables document](kalico/Save_Variables.md) for more details
on how Trad Rack uses save_variables.

## Bowden speeds

There is more force required and more inertia when loading filament
when the buffer is empty than when the buffer is full: in the former
case the drive gears must rotate the spool, but in the latter case the
spool can stay stationary since all the loaded filament comes out of
the buffer. To take advantage of this, we have two separate speeds
that are used when moving filament through the bowden tube:

- `spool_pull_speed` (mm/s): this speed is used when loading from a
  lane whose buffer is assumed to be empty (usually because the lane's
  filament has not been unloaded from the toolhead previously).
- `buffer_pull_speed` (mm/s): this speed is used when unloading or
  when loading from a lane whose buffer is assumed to be full (because
  the lane's filament has been unloaded from the toolhead previously).

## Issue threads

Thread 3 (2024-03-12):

Internal error during connect: module 'toolhead' has no attribute 'BUFFER_TIME_HIGH'

MRX8024, 2024-03-12:
Hi, I faced this problem on 11 klipper. What do you recommend other than updating?

  File "/home/klipper/klippy/extras/trad_rack.py", line 2256, in load_config
    return TradRack(config)
  File "/home/klipper/klippy/extras/trad_rack.py", line 41, in __init__
    self.tr_toolhead = TradRackToolHead(
  File "/home/klipper/klippy/extras/trad_rack.py", line 1742, in __init__
    self.move_queue.set_flush_time(toolhead.BUFFER_TIME_HIGH)

Thanks
-Maxim

rsghosh, 2024-03-14:
If you switch to the `pre_toolhead_changes` branch I think it will work; the version of `trad_rack.py` on this branch is meant to be compatible with older versions of Klipper from before [commit bafb126](https://github.com/Klipper3d/klipper/commit/bafb126abd77edd0cb2e5ae3b5d99ff83272594c) (which was when `toolhead.BUFFER_TIME_HIGH` was added). You can switch to this branch using the following commands:
```
cd ~
./trad_rack_klippy_module/Klipper_Stuff/klippy_module/install.sh pre_toolhead_changes
sudo systemctl restart klipper
```
Let me know if this fixes it for you.

In the future, please use the `#tr_build_help` channel on the [Annex Discord server](https://discord.gg/MzTR3zE) for troubleshooting issues, as we have more people active there and you will likely get responses faster.

-Ryan

MRX8024, 2024-03-14:
Yes, thanks, I replaced the program file and it helped. I've been using Tradrak for a long time, just wanted to update foruse Belay. Thanks for your hard work! I appreciate it/

-Maxim

Closed 2024-03-14.

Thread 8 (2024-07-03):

Heat inserts too loose

dfosantos, 2024-07-03:
M3 heat inserts usually have an outer diameter of 4.6mm.
Current diameter of the designed parts for the heat inserts is 4.7mm, which makes it too loose.

I suggest changing to 4.5mm, as tighter is better than loose. Heat insert can always melt the plastic.

rsghosh, 2024-07-11:
The printed parts are designed for heat inserts with a 5.0mm outer diameter and 4.0mm length. You can find recommended sources for the inserts in the Trad Rack BOM/sourcing guide: https://docs.google.com/spreadsheets/d/1SKBtkgSVPqqGEjftI6v6i6T5Bh3Phx-4YXsJYH17ggs/edit?usp=sharing

(Vendors that sell parts for DIY 3D printers also often carry the same M3x5x4mm inserts as the AliExpress source from the guide)

Closed 2024-07-11.

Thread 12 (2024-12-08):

Section 'trad_rack' is not a valid config section

BennyBenasy, 2024-12-08:
I encountered this problem and can't fix it. I install the klippy module according to the instructions

rsghosh, 2024-12-12:
Did you do `sudo systemctl restart klipper` after installing the module?

If that doesn't fix it, please make a post in the [Annex Discord server](https://discord.gg/MzTR3zE) in the `tr_build_help` channel and attach your klippy.log file.

Closed 2025-04-21.

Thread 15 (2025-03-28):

[FR] have option for pre soldered enstop PCBs for tradrack endstop

Nathan22211, 2025-03-28:
right now, in the current design, you pretty much have to buy pre-soldered endstops with wire, or solder them yourself. The latter isn't easy when you don't have steady hands. Using endstop PCB meant for something like an ender 3 might help with accessibility in building the tradrack, as well as help with repairability. It would only require crimping a few times rather than repeated soldering in the event of n endstop failure.

rsghosh, 2025-04-21:
Thanks for the feedback. Unfortunately I don't think we'll be able to fit that PCB inside the selector with the current design since the belt is very close by.

If you are having trouble soldering the wires onto the endstops, I'd recommend trying the "D3" variant of the endstop switch (D2F-L-D3 for the variant with a lever and D2F-D3 for the variant without). This version has terminals with a hole, so you can thread the wire through the hole and wrap it back around itself before soldering. This way you at least don't need to worry about accidentally knocking the wire and switch terminal out of alignment with each other while soldering since they will already be secured to each other.

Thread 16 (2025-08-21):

Repo has untracked source files: ['klippy/extras/belay.py', 'klippy/extras/gcode_shell_command.py', 'klippy/extras/trad_rack.py']

dadoblu2000, 2025-08-21:
After updating to Klipper v0.13.0-219-g3a11645a, I get the following message, and I can't start Klipper because it gives me the following error: Klipper Reports: ERROR

Section 'trad_rack' is not a valid config section

Once the underlying issue is corrected, use the "RESTART"
command to reload the config and restart the host software.
Printer is halted.

Any advice?

[klippy (14).log](https://github.com/user-attachments/files/21926299/klippy.14.log)

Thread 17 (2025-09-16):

Internal error during connect: 'TradRackToolHead' object has no attribute '_flush_handler'

IRBnemez, 2025-09-16:
After update to Klipper v0.13.0-268-gc7365c8c I get the following message:
`Klipper reports: ERROR

Internal error during connect: 'TradRackToolHead' object has no attribute '_flush_handler'

Once the underlying issue is corrected, use the "RESTART"
command to reload the config and restart the host software.
Printer is halted`

When I comment [include trad_rack.cfg] from the printer.cfg the printer starts fine

[klippy.log.txt](https://github.com/user-attachments/files/22366846/klippy.log.txt)

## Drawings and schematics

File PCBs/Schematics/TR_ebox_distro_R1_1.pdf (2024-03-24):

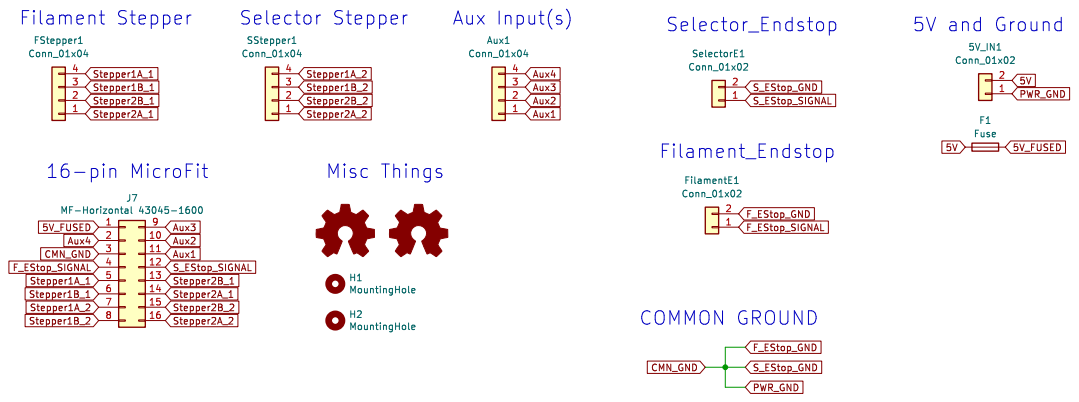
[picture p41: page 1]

Id: 1/1 Title: File: carabiner.kicad_sch Sheet: /

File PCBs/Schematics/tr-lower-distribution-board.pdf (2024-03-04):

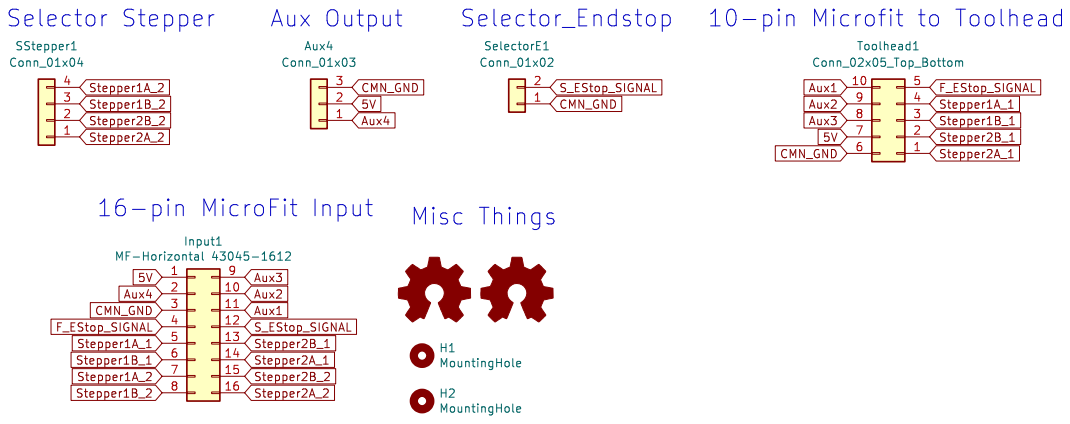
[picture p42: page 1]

Id: 1/1 Title: File: tr-lower-carabiner-distribution-board.kicad_sch Sheet: /

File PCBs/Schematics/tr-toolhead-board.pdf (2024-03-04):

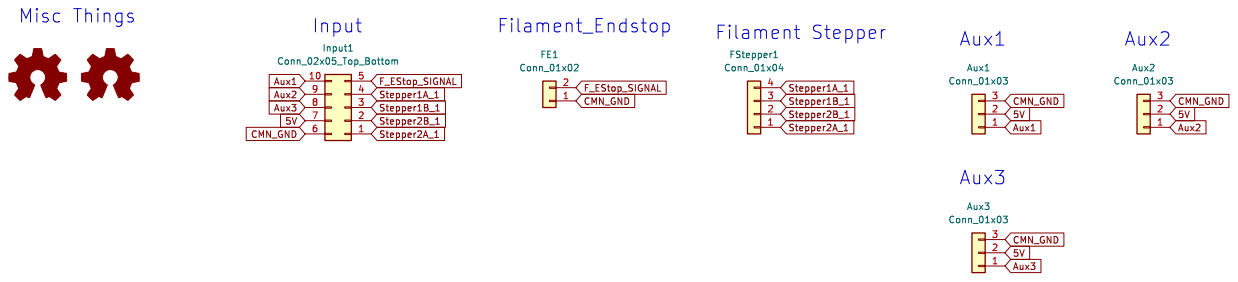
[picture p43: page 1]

Id: 1/1 Title: File: tr-toolhead-board.kicad_sch Sheet: /

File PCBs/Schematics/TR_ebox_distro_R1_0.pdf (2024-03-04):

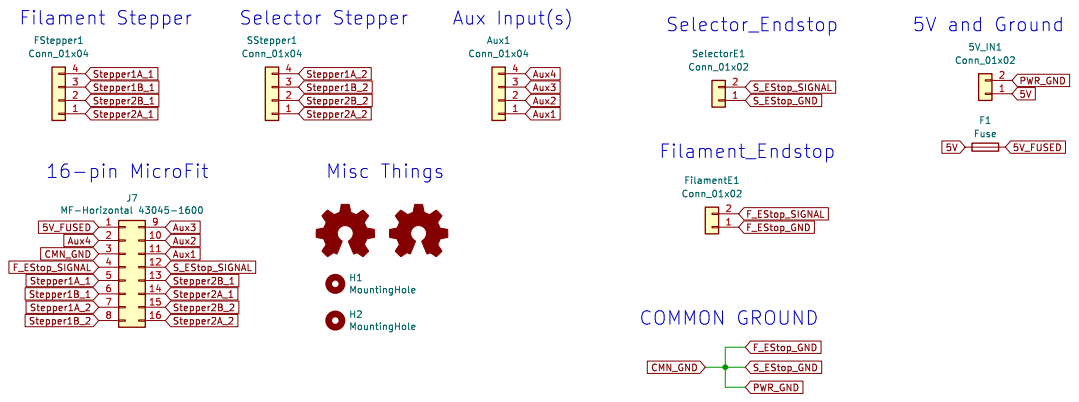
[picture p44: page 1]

Id: 1/1 Title: File: carabiner.kicad_sch Sheet: /

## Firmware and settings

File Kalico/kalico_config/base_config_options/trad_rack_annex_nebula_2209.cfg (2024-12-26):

# Nebula - 2209 drivers (UART mode)

# DIP switch
# 1 - off   (use ES0 instead of STEP0 DIAG)
# 2 - off   (use ES1 instead of STEP1 DIAG)
# 3 - off   (use UART for STEP0)
# 4 - off   (use UART for STEP1)

[mcu tr]
serial:

[trad_rack]
selector_max_velocity: 400
selector_max_accel: 10000
toolhead_fil_sensor_pin: ^!PA1
lane_count: 14
lane_spacing: 17.0
servo_down_angle: 0.0
servo_up_angle: 131.0
toolhead_unload_speed: 20
extruder_load_speed: 20
toolhead_sense_speed: 20
selector_unload_length: 17.5
bowden_length: 700.0
extruder_load_length: 44.5
hotend_load_length: 6.0
toolhead_unload_length: 40.0
buffer_pull_speed: 100.0    # increase this to 300+ once you are ready
                            # (but some motors may not be able to handle this).

[stepper_tr_selector]
# stepper connected to STEP0, endstop to ES0
step_pin: tr:STEP0_STEP
dir_pin: !tr:STEP0_DIR
enable_pin: !tr:STEP0_EN
rotation_distance: 40
microsteps: 16
full_steps_per_rotation: 200
endstop_pin: ^tr:ES0
position_min: 0.0
position_endstop: 0.0
position_max: 221   # (lane_count - 1) * lane_spacing
homing_speed: 30

[stepper_tr_fil_driver]
# stepper connected to STEP1, selector filament sensor to ES1
step_pin: tr:STEP1_STEP
dir_pin: !tr:STEP1_DIR
enable_pin: !tr:STEP1_EN
rotation_distance: 22.67895
gear_ratio: 50:17
microsteps: 16
full_steps_per_rotation: 200
endstop_pin: ^tr:ES1    # selector filament sensor
position_min: -5000
position_endstop: 0
position_max: 5000
homing_positive_dir: False

[tmc2209 stepper_tr_selector]
# connected to STEP0
uart_pin: tr:STEP0_UART
interpolate: True
run_current: 0.63   # for a 1A peak motor
sense_resistor: 0.110

[tmc2209 stepper_tr_fil_driver]
# connected to STEP1
uart_pin: tr:STEP1_UART
interpolate: False
run_current: 1.27   # for a 2A peak motor
sense_resistor: 0.110

[servo tr_servo]
# connected to SER0
pin: tr:SER0
maximum_servo_angle: 131
minimum_pulse_width: 0.000700
maximum_pulse_width: 0.002200

[extruder]
max_extrude_only_distance: 200
max_extrude_cross_section: 100

[board_pins nebula_aliases]
mcu: tr
aliases:
    # stepper driver 0
    STEP0_STEP=gpio7,
    STEP0_DIR=gpio6,
    STEP0_EN=gpio8,
    STEP0_UART=gpio20, STEP0_CS=gpio20,

    # stepper driver 1
    STEP1_STEP=gpio3,
    STEP1_DIR=gpio2,
    STEP1_EN=gpio4,
    STEP1_UART=gpio21, STEP1_CS=gpio21,

    # endstops
    ES0=gpio0,
    ES1=gpio1,

    # servos
    SER0=gpio22,
    SER1=gpio14,

    # IO cluster
    IO0=gpio17,
    AIO0=gpio26,
    AIO1=gpio27,
    AIO2=gpio28,

    # expander 1 (slot on left side)
    EXP1_2=GND,     EXP1_1=<X>,
    EXP1_4=gpio0,   EXP1_3=<RST>,
    EXP1_6=gpio1,   EXP1_5=gpio11,
    EXP1_8=gpio5,   EXP1_7=gpio13,
    EXP1_10=gpio12, EXP1_9=gpio10,

    # expander 2 (slot on left side)
    EXP2_2=<GND>,   EXP2_1=<5V>,
    EXP2_4=<X>,     EXP2_3=<X>,
    EXP2_6=<X>,     EXP2_5=<X>,
    EXP2_8=<X>,     EXP2_7=<X>,
    EXP2_10=<X>,    EXP2_9=gpio9

# Macros
[gcode_macro ACTIVATE_EXTRUDER]
rename_existing: ACTIVATE_EXTRUDER_BASE
gcode:
    {% set EXTRUDER = params.EXTRUDER|default('extruder')|lower|replace('extruder', '') %}
    {% if EXTRUDER == '' %}
        {% set EXTRUDER = '0' %}
    {% endif %}
    TR_LOAD_TOOLHEAD LANE={EXTRUDER}

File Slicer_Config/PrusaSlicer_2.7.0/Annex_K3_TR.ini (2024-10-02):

# Print profiles for K3 with Trad Rack.
# Meant for use with PrusaSlicer 2.7.0

[vendor]
repo_id = non-prusa-fff
# Vendor name will be shown by the Config Wizard.
name = Annex Engineering
config_version = 0.1.8

[printer_model:K3_TR]
name = K3 Dual 4010 Trad Rack
variants = 0.4
technology = FFF
family = K3 Trad Rack
default_materials = K3 TR ASA

[printer_model:K3F_TR]
name = K3 Frostbite Trad Rack
variants = 0.4
technology = FFF
family = K3 Trad Rack
default_materials = K3F TR ASA; K3F TR PLA

[print:*common*]
avoid_crossing_curled_overhangs = 1
avoid_crossing_perimeters = 0
avoid_crossing_perimeters_max_detour = 0
bottom_fill_pattern = monotonic
bottom_solid_layers = 5
bottom_solid_min_thickness = 0
bridge_acceleration = 10000
bridge_angle = 0
bridge_flow_ratio = 0.9
bridge_speed = 60
brim_separation = 0.1
brim_type = outer_only
brim_width = 0
compatible_printers = 
complete_objects = 0
default_acceleration = 15000
dont_support_bridges = 0
draft_shield = disabled
elefant_foot_compensation = 0.15
enable_dynamic_overhang_speeds = 1
external_perimeter_acceleration = 0
external_perimeter_extrusion_width = 0
external_perimeter_speed = 150
external_perimeters_first = 0
extra_perimeters = 0
extra_perimeters_on_overhangs = 0
extruder_clearance_height = 20
extruder_clearance_radius = 20
extrusion_width = 0.42
fill_angle = 45
first_layer_acceleration = 10000
first_layer_acceleration_over_raft = 0
first_layer_extrusion_width = 0
first_layer_height = 0.2
first_layer_speed = 100
first_layer_speed_over_raft = 30
fuzzy_skin = none
fuzzy_skin_point_dist = 0.8
fuzzy_skin_thickness = 0.3
gap_fill_enabled = 1
gap_fill_speed = 175
gcode_comments = 0
gcode_label_objects = firmware
gcode_resolution = 0.002
gcode_substitutions = "(SET_PRESSURE_ADVANCE ADVANCE=[0.]+)\\n";"Save_Pressure_Advance\\n${1}\\n";r;"Save PA before ramming"
infill_acceleration = 15000
infill_anchor = 2.5
infill_anchor_max = 12
infill_every_layers = 1
infill_extruder = 1
infill_extrusion_width = 0.5
infill_first = 0
infill_only_where_needed = 0
infill_overlap = 10%
infill_speed = 250
interface_shells = 0
ironing = 0
ironing_flowrate = 15%
ironing_spacing = 0.1
ironing_speed = 15
ironing_type = top
layer_height = 0.2
max_print_speed = 300
max_volumetric_extrusion_rate_slope_negative = 0
max_volumetric_extrusion_rate_slope_positive = 0
max_volumetric_speed = 35
min_bead_width = 85%
min_feature_size = 25%
min_skirt_length = 4
mmu_segmented_region_max_width = 0
notes = 
only_retract_when_crossing_perimeters = 0
ooze_prevention = 0
overhang_speed_0 = 55%
overhang_speed_1 = 60%
overhang_speed_2 = 80%
overhang_speed_3 = 90%
overhangs = 1
perimeter_acceleration = 10000
perimeter_extruder = 1
perimeter_extrusion_width = 0
perimeter_generator = arachne
perimeter_speed = 200
post_process =
print_settings_id =
raft_contact_distance = 0.1
raft_expansion = 1.5
raft_first_layer_density = 90%
raft_first_layer_expansion = 3
raft_layers = 0
resolution = 0.002
seam_position = aligned
single_extruder_multi_material_priming = 0
skirt_distance = 2
skirt_height = 1
skirts = 1
slice_closing_radius = 0.049
slicing_mode = regular
small_perimeter_speed = 50%
solid_infill_acceleration = 0
solid_infill_every_layers = 0
solid_infill_extruder = 1
solid_infill_extrusion_width = 0
solid_infill_speed = 200
spiral_vase = 0
staggered_inner_seams = 0
standby_temperature_delta = -5
support_material = 0
support_material_angle = 0
support_material_auto = 0
support_material_bottom_contact_distance = 0
support_material_bottom_interface_layers = -1
support_material_buildplate_only = 1
support_material_closing_radius = 2
support_material_contact_distance = 0.2
support_material_enforce_layers = 0
support_material_extruder = 1
support_material_extrusion_width = 0.4
support_material_interface_contact_loops = 0
support_material_interface_extruder = 1
support_material_interface_layers = 0
support_material_interface_pattern = rectilinear
support_material_interface_spacing = 0
support_material_interface_speed = 100%
support_material_pattern = rectilinear
support_material_spacing = 2
support_material_speed = 100
support_material_style = organic
support_material_synchronize_layers = 0
support_material_threshold = 0
support_material_with_sheath = 0
support_material_xy_spacing = 0.6
support_tree_angle = 40
support_tree_angle_slow = 25
support_tree_branch_diameter = 2
support_tree_branch_diameter_angle = 5
support_tree_branch_diameter_double_wall = 0
support_tree_tip_diameter = 0.8
support_tree_top_rate = 30%
thick_bridges = 0
thin_walls = 1
threads = 20
top_fill_pattern = monotoniclines
top_infill_extrusion_width = 0.4
top_solid_infill_acceleration = 0
top_solid_infill_speed = 100
top_solid_layers = 6
top_solid_min_thickness = 0
travel_speed = 400
travel_speed_z = 0
wall_distribution_count = 1
wall_transition_angle = 10
wall_transition_filter_deviation = 25%
wall_transition_length = 100%
wipe_tower = 1
wipe_tower_bridging = 10
wipe_tower_brim_width = 2
wipe_tower_cone_angle = 25
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

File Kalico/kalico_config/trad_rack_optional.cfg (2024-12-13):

[trad_rack]
# optional custom gcode
pre_unload_gcode:
    SAVE_GCODE_STATE NAME=PRE_UNLOAD_state
    {% set use_wiper = printer["gcode_macro TR_Variables"].use_wiper %}
    {% if printer.virtual_sdcard.is_active %}
        {% set z_max = printer.toolhead.axis_maximum.z - printer.gcode_move.homing_origin.z %}
        {% set z_lift = printer["gcode_macro TR_Variables"].z_lift|float %}
        {% set x_park = printer["gcode_macro TR_Variables"].x_park|float %}
        {% set y_park = printer["gcode_macro TR_Variables"].y_park|float %}
        {% set do_x_park = printer["gcode_macro TR_Variables"].do_x_park %}
        {% set do_y_park = printer["gcode_macro TR_Variables"].do_y_park %}
        {% set st = printer["gcode_macro TR_Variables"].travel_speed * 60 %}
        {% set shape_tip = printer["gcode_macro TR_Variables"].shape_tip %}
        {% set x = printer.gcode_move.gcode_position.x %}
        {% set y = printer.gcode_move.gcode_position.y %}
        {% set z = printer.gcode_move.gcode_position.z %}
        {% set z_park = [z + z_lift, z_max]|min %}
        
        SET_GCODE_VARIABLE MACRO=TR_Variables VARIABLE=x VALUE={x}
        SET_GCODE_VARIABLE MACRO=TR_Variables VARIABLE=y VALUE={y}
        SET_GCODE_VARIABLE MACRO=TR_Variables VARIABLE=z VALUE={z}
        SET_GCODE_VARIABLE MACRO=TR_Variables VARIABLE=saved_pos VALUE={True}
        SET_GCODE_VARIABLE MACRO=TR_Variables VARIABLE=z_park VALUE={z_park}

        # lift z
        G90                     # absolute positioning
        G1 Z{z_park}            # move to z position

        # move to purge location
        {% if use_wiper %}
            Go_To_Purge_Location

        # park x and y
        {% else %}
            G90                 # absolute positioning
            {% if do_x_park %}
                {% set x = x_park %}
            {% endif %}
            {% if do_y_park %}
                {% set y = y_park %}
            {% endif %}
            G1 X{x} Y{y} F{st}  # move to x and y position
        {% endif %}

        # shape filament tip
        {% if shape_tip %}
            Shape_Tip
        {% endif %}
    {% else %}
        # move to purge location
        {% if use_wiper %}
            Go_To_Purge_Location
        {% endif %}

        # shape filament tip
        Shape_Tip
    {% endif %}
    RESTORE_GCODE_STATE NAME=PRE_UNLOAD_state

post_load_gcode:
    SAVE_GCODE_STATE NAME=POST_LOAD_state
    {% set use_wiper = printer["gcode_macro TR_Variables"].use_wiper %}
    {% if printer.virtual_sdcard.is_active %}
        {% set st = printer["gcode_macro TR_Variables"].travel_speed * 60 %}
        {% set take_frame = printer["gcode_macro TR_Variables"].take_frame %}
        {% set x = printer["gcode_macro TR_Variables"].x %}
        {% set y = printer["gcode_macro TR_Variables"].y %}
        {% set z = printer["gcode_macro TR_Variables"].z %}
        {% set saved_pos = printer["gcode_macro TR_Variables"].saved_pos %}
        {% set z_park = printer["gcode_macro TR_Variables"].z_park %}

        # take timelapse frame
        {% if take_frame %}
            TIMELAPSE_TAKE_FRAME
        {% endif %}

        # wipe nozzle
        {% if use_wiper %}
            Home_and_Wipe_Nozzle
        {% endif %}

        # move to pre-toolchange position
        {% if saved_pos %}
            G90                     # absolute positioning
            G1 Z{z_park}            # restore z parking position
            G1 X{x} Y{y} F{st}      # restore original x and y position
            G1 Z{z}                 # restore original z position
            SET_GCODE_VARIABLE MACRO=TR_Variables VARIABLE=saved_pos VALUE={False}
        {% endif %}

        Restore_Pressure_Advance    # restore PA from before ramming
    {% elif use_wiper %}
        Home_and_Wipe_Nozzle
    {% endif %}
    RESTORE_GCODE_STATE NAME=POST_LOAD_state

[gcode_macro TR_Variables]
description: Variables for use with Trad Rack pre unload and post load gcode
variable_z_lift:        0.1     # distance to lift z axis before toolchange
variable_x_park:        0.0     # x position to park before unloading
variable_y_park:        175.0   # y position to park before unloading
variable_do_x_park:     False   # whether to park x before unloading
variable_do_y_park:     False   # whether to park y before unloading
variable_travel_speed:  300     # how fast travel speeds will be performed
variable_shape_tip:     False   # whether to add tip-shaping gcode on unload during printing
                                # (set to False if you are using ramming from the slicer)
variable_take_frame:    False   # whether to take a timelapse frame after each toolchange
                                # requires: https://github.com/mainsail-crew/moonraker-timelapse
                                # (use "layermacro" mode)
variable_use_wiper:     False   # intended for the Annex K3 printer and requires
                                # Go_To_Purge_Location and Wipe_Nozzle gcode
                                # macros. Makes the toolchange occur over the
                                # purge bucket and wipes the nozzle before
                                # resuming the print. Variables relating to
                                # parking will be ignored if this is set to True
# don't change any of the variables below this line
variable_x:             0
variable_y:             0
variable_z:             0
variable_saved_pos:     False
variable_z_park:        0
gcode:

[gcode_macro Shape_Tip]
description: Perform tip-shaping, retraction, and cooling moves
gcode:
    SAVE_GCODE_STATE NAME=Shape_Tip_state
    Save_Pressure_Advance

    Slicer_Unload   # replace this with a different macro/gcode
                    # to change unloading

    Restore_Pressure_Advance
    RESTORE_GCODE_STATE NAME=Shape_Tip_state

[gcode_macro Set_Slicer_Unload_Preset]
description: Apply a preset of values to use for the Slicer_Unload macro
# params:
#   PRESET  Name of the preset to apply. Must match one of the variables below.
# see gcode_macro Slicer_Unload for variables that can be changed in a preset

# SuperSlicer presets
variable_asa_ss = {
    "filament_ramming_parameters": "120 110 5.32258 5.45161 5.67742 6 6.48387 7.12903 7.90323 8.70968 9.3871 9.83871 10.0968 10.2258| 0.05 5.30967 0.45 5.50967 0.95 6.1871 1.45 7.39677 1.95 9.05484 2.45 10 2.95 10.3098 3.45 13.0839 3.95 7.6 4.45 7.6 4.95 7.6",
    "superslicer": True}
variable_pla_ss = {
    "filament_ramming_parameters": "130 120 2.70968 2.93548 3.32258 3.83871 4.58065 5.54839 6.51613 7.35484 7.93548 8.16129| 0.05 2.66451 0.45 3.05805 0.95 4.05807 1.45 5.97742 1.95 7.69999 2.45 8.1936 2.95 11.342 3.45 11.4065 3.95 7.6 4.45 7.6 4.95 7.6",
    "superslicer": True}

# PrusaSlicer presets
variable_asa_ps = {
    "filament_ramming_parameters": "120 110 5.32258 5.45161 5.67742 6 6.48387 7.12903 7.90323 8.70968 9.3871 9.83871 10.0968 10.2258| 0.05 5.30967 0.45 5.50967 0.95 6.1871 1.45 7.39677 1.95 9.05484 2.45 10 2.95 10.3098 3.45 13.0839 3.95 7.6 4.45 7.6 4.95 7.6",
    "superslicer": False}
variable_pla_ps = {
    "filament_ramming_parameters": "130 120 2.70968 2.93548 3.32258 3.83871 4.58065 5.54839 6.51613 7.35484 7.93548 8.16129| 0.05 2.66451 0.45 3.05805 0.95 4.05807 1.45 5.97742 1.95 7.69999 2.45 8.1936 2.95 11.342 3.45 11.4065 3.95 7.6 4.45 7.6 4.95 7.6",
    "superslicer": False}

# presets should follow the format below:
# variable_<preset_name_in_lowercase> = {
#     "<variable1_name>": <variable1_value>,
#     "<variable2_name>": <variable2_value>,
#     "<variable3_name>": <variable3_value>}
gcode:
    {% set preset_name = params.PRESET|lower %}
    {% if preset_name in printer['gcode_macro Set_Slicer_Unload_Preset'] %}
        {% set preset = printer['gcode_macro Set_Slicer_Unload_Preset'][preset_name] %}
        {% for key in preset %}
            SET_GCODE_VARIABLE MACRO=Slicer_Unload VARIABLE={key} VALUE={preset[key]}
        {% endfor %}
    {% else %}
        { action_raise_error("Preset \"%s\" does not exist" % preset_name) }
    {% endif %}

[gcode_macro Slicer_Unload]
# logic based on WipeTower::toolchange_Unload() from PrusaSlicer and SuperSlicer
description: Mimic ramming and unload behavior of PrusaSlicer or SuperSlicer
# params:
#   NEW_TEMPERATURE     extruder temperature to set (optional; only needs to be
#                       passed if the new filament requires a different
#                       temperature than the current temperature target)

# printer settings
variable_cooling_tube_length = 14
variable_cooling_tube_retraction = 30
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

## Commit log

2023-02-15 Add existing files for beta
    [[a]_arm_x1_rev2.STL, [a]_endstop_cover_x1_rev1.STL, [a]_microfit_holder_(9g_servo)_x1_rev1.STL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]
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2023-02-19 Add 1st 15 numbered collet clips
    [[a]_number_0_collet_clip_x1_rev1.STL, [a]_number_10_collet_clip_x1_rev1.STL, [a]_number_5_collet_clip_x1_rev1.STL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]
2023-02-19 Add collet clips 15-19
    [[a]_number_15_collet_clip_x1_rev1.STL, number_16_collet_clip_x1_rev1.STL, number_17_collet_clip_x1_rev1.STL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]
2023-02-19 collet clips no longer marked as experimental
    [[a]_number_0_collet_clip_x1_rev1.STL, [a]_number_10_collet_clip_x1_rev1.STL, [a]_number_15_collet_clip_x1_rev1.STL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]
2023-02-20 Fix import error, compatibility after last_kin_flush_time got renamed to force_flush_time
    [trad_rack.py]
2023-02-20 Use a safer starting value for buffer_pull_speed
    [trad_rack_skr_pico.cfg]
2023-02-20 Bosch extrusion compatibility fix: reduce printed part intrusion from 1.0mm to 0.5mm and screw intrusion from 5.0mm to 4.5mm
    [[a]_rail_stop_mgn9_x1_rev1.STL, [a]_rail_stop_mgn9_x1_rev2.STL, k3_side_mount_left_x1_rev1.STL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]
2023-02-24 Add slicer configs and documentation Clarify servo pin Minor documentation fixes
    [trad_rack_skr_pico.cfg]
2023-02-24 Fix link to stl folder
2023-02-25 Add option to use K3 wiper during toolchange
    [trad_rack_optional.cfg]
2023-02-27 Add sherpa mini and micro with sensor and collet support
    [idler_arm_long_hd_sensor_x1_rev1.STL, idler_arm_long_sensor_x1_rev1.STL, sherpa_mini_ecas_sensor_x1_rev1.STL]
2023-02-27 Enlarge M5 counterbores from 10mm to 10.4mm to fit washers
    [k3_side_mount_left_x1_rev2.STL, k3_side_mount_left_x1_rev3.STL, k3_side_mount_right_x1_rev2.STL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]
2023-02-27 Arm: Increase slot diameter from 10.10 to 10.15mm, more material around heatset
    [[a]_arm_x1_rev2.STL, [a]_arm_x1_rev3.STL]
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2023-03-02 Add rail installation tool
    [rail_installation_guide_x2_rev1.stl]
2023-03-02 Make naming more consistent
    [trad_rack_optional.cfg, trad_rack_skr_pico.cfg]
2023-03-23 Add RIDGA parts, move experimental folder
    [[a]_microfit_holder_(9g_servo)_x1_rev1.STL, carriage_left_(ridga)_x1_rev1.STL, carriage_right_(9g_servo)_x1_rev2.STL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]
2023-03-25 Use wiper regardless of whether a print is in progress
    [trad_rack_optional.cfg]
2023-03-29 - increase outward gear mesh travel (changed from 0.35mm to 0.70mm) - increase spacing of heatsets around 50T gear to avoid bulging plastic interfereing with the gear - increase thickness of sides of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
    [[a]_arm_x1_rev3.STL, [a]_arm_x1_rev4.STL, carriage_left_(ridga)_x1_rev1.STL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]
2023-03-29 Add 6mm collet version of sherpa micro housing from ZZToP Make filenames more consistent Add readme explaining collet types in filenames
    [housing_core_(ecas)_(sensor)_x1_rev1.STL]
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2023-04-04 Always home x and y if needed before trying to wipe the nozzle
    [trad_rack_optional.cfg]
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2023-04-11 Don't move after load if a position wasn't saved
    [trad_rack_optional.cfg]
2023-04-13 Add servo jig instructions Add FORCE parameter for TR_SERVO_DOWN Mention RESET_SPEED parameter in documentation for TR_LOAD_LANE
    [trad_rack.py]
2023-04-14 Increase slot height clearance from 0.4mm to 0.6mm to increase leniency on bridging
2023-04-14 Increase chamfer size on locating pins to make room for top layer over-extrusion
    [[a]_endstop_cover_x1_rev1.STL, [a]_endstop_cover_x1_rev2.STL]
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2023-04-26 Change downward gear travel from 0.5mm to 0.9mm, upward gear travel from 0.6mm to 0.4mm
    [[a]_arm_x1_rev4.STL, [a]_arm_x1_rev5.STL, gear_casing_left_x1_rev4.STL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]
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2023-04-30 Flush step generation for both toolheads on extruder sync/unsync (fixes an issue where the extruder would sometimes not sync)
    [trad_rack.py]
2023-05-04 Decrease chances of cracking around ECAS04 coupling >> (increased thickness and added cutouts similar to crush ribs)
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2023-05-21 Add configurable macro to mimic prusaslicer and superslicer ramming and unloading
    [trad_rack_optional.cfg]
2023-05-26 Make negative extrusion moves go in the right direction
    [trad_rack_optional.cfg]
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2023-05-28 Revert only updating bowden lengths if the sensor was not reached early
    [trad_rack.py]
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2023-06-07 Add missing brackets
2023-06-12 Added [save_variables] functionality for load/unload bowden lengths and lane status. Updates some documentation to reflect the changes.
    [trad_rack_skr_pico.cfg, trad_rack_vars.cfg]
2023-06-12 Update trad_rack.py
    Moved config bowden length check to TR_HOME because that virtually always has to run at least once. Unfortunately, cannot put in handle_connect() due to a gcode not being an instance of TradRack error. No gcode commands can be run from handle_connect.
    [trad_rack.py]
2023-06-12 Update Klipper_Stuff/klipper_config/trad_rack_skr_pico.cfg
    Remove [save_variables] from trad_rack_skr_pico.cfg in case user already has [save_variables] defined elsewhere.
    [trad_rack_skr_pico.cfg]
2023-06-13 Added klippy:ready event handler to call `_load_saved_state` per @rsghosh suggestion. Removed `TR_CHECK_LANES` and references to `lanes_alive` for implementation in tool grouping branch. Reverting `_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
    [trad_rack.py]
2023-06-23 Delete trad_rack_vars.cfg
    Should no longer be needed.
    [trad_rack_vars.cfg]
2023-06-27 Restore z parking position in case it changed during wiping
    [trad_rack_optional.cfg]
2023-06-27 Redo microfit holder (stronger and includes 2-pin connector for filament sensor)
    [[a]_microfit_holder_x1_rev1.STL]
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2023-06-28 Add 9g servo version of new microfit holder
    [[a]_microfit_holder_(9g_servo)_x1_rev1.STL]
2023-06-28 Updated error message for [save_variables
    [trad_rack.py]
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2023-07-02 Remove bowden_unload_length_mod config option, set a lower example bowden_length
    [trad_rack_skr_pico.cfg]
2023-07-07 Whitespace and readability fixes
    [trad_rack.py]
2023-07-11 Fix typo from 174c837
    [trad_rack_optional.cfg]
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2023-07-12 Fix check for whether to park x and y
    [trad_rack_optional.cfg]
2023-07-28 add default speeds to config (aka expose more config options)
    [trad_rack_nebula_2209.cfg, trad_rack_nebula_5160.cfg, trad_rack_skr_pico.cfg]
2023-08-03 Check lane before trying to reset lane speed
    [trad_rack.py]
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2023-08-22 Fix slicer profile version
    [Annex_K3_TR.ini]
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2023-09-14 Add back fix from 77a1232 that was in main
    [trad_rack.py]
2023-09-22 - Don't base filament_max_accel default on max_extrude_only_accel - Respect extruder velocity and accel limits on any move involving the extruder - Apply velocity and acceleration limits correctly wh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
    [trad_rack.py]
2023-09-24 Use correct velocity and accel limits for filament moves (respects extruder limits)
    [trad_rack.py]
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2023-09-24 Fix spi_bus value
    [trad_rack_nebula_5160.cfg]
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2023-09-30 Fix TR_LOAD_TOOLHEAD optional parameters not working with T0, T1, T2, etc.
    [trad_rack.py]
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2023-10-01 Check selector is homed before setting extruder temperature to avoid extra waiting
    [trad_rack.py]
2023-10-02 - Increase retract_before_travel to avoid retractions in Monotonic Lines top infill - Remove TR_Print_Start macro in favor of using T<index> commands with the MIN_TEMP parameter
    [trad_rack_optional.cfg]
2023-10-02 Call Go_To_Purge_Location in pre_unload_gcode outside of prints too
    [trad_rack_optional.cfg]
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2023-10-03 Finish handling case where the selected tool doesn't have a lane assigned to it
    [trad_rack.py]
2023-10-03 Add missing entry for runout resume callback
    [trad_rack.py]
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2023-10-10 Left and right selector carriage changes: - Raise top of belt return path to match change made to the middle carriage from 506e9c4 - Raise bottom surfaces by 0.1mm to avoid contact with h-cart - Add 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
    [carriage_left_(ridga)_x1_rev2.STL, carriage_left_(ridga)_x1_rev3.STL, carriage_left_x1_rev5.STL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]
2023-10-18 Printed part improvements: - idler mount: - extended front inward to cover T-nuts and engage more with the extrusion slot - changed extrusion slot protrusions to match lane module (non-angled for bet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
    [[a]_endstop_cover_x1_rev2.STL, [a]_endstop_cover_x1_rev3.STL]
2023-10-18 Ensure toolhead is unloaded after a runout even if filament is not detected (fixes bug introduced by bb1062b)
    [trad_rack.py]
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2023-10-24 Use a more realistic nominal servo angle, more generic starting value for maximum_pulse_width
    [trad_rack_nebula_2209.cfg, trad_rack_nebula_5160.cfg, trad_rack_skr_pico.cfg]
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2023-10-25 - Move extruder/filament driver syncing to a separate class - Add the ability to sync the filament driver to the extruder (the reverse was already implemented and used during toolhead loads/unloads)
    [trad_rack.py]
2023-10-25 Fix mistake from merge bbf22d8
    [trad_rack.py]
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2023-10-27 - Store just rotation distance instead of tuple - Fix case where the filament driver is not synced but the extruder sync sensor still tries to disable itself
    [trad_rack.py]
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2023-11-05 - Add customization document - Add filament settings to slicing document - Other documentation fixes
2023-11-05 Fix link and list customization doc under klipper section
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2023-11-19 - Support syncing during reverse extrusion - Simplify enable and disable events and ensure consistent behavior whether tip shaping comes from the gcode file or pre_unload_gcode - Replace verbose opti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
    [trad_rack.py]
2023-11-22 Remove step generator from original toolhead when syncing (solves stepcompress error when using TR_SERVO_UP or TR_SERVO_DOWN in the middle of a print with sync_to_extruder set to True)
    [trad_rack.py]
2023-11-22 Fix case where lane 0 is assigned as the active lane
    [trad_rack.py]
2023-11-22 Round lane_spacing before calculating new lane positions (ensures position_max accounts for accumulated error from rounding)
    [trad_rack.py]
2023-11-28 - First draft of printer and hardware requirements doc - Other minor doc fixes
2023-11-28 Use more generic initial min and endstop position
    [trad_rack_annex_nebula_2209.cfg, trad_rack_annex_nebula_5160.cfg, trad_rack_btt_mmb.cfg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]
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2023-12-07 Small fixes, add tr prefix to remaining variables that are saved to disk
    [trad_rack_optional.cfg]
2023-12-07 Increase left carriage contact area with microswitch plunger
    [carriage_left_x1_rev6.STL, carriage_left_x1_rev7.STL]
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2023-12-09 Move toothed side of left belt slot 0.1mm farther from the smooth side to make belt fitment less tight (smallest width changed from 0.75mm to 0.85mm)
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2023-12-12 Add guide on what STLs to print, other small fixes
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2023-12-27 Fix case where resume_callback gets reset to None prematurely if TR_RESUME is used multiple times during a pause caused by a runout
    [trad_rack.py]
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2024-01-03 Fix regression introduced in ec8d1d2 that would cause klipper to shut down if a load error occurred when calling TR_RESUME
    [trad_rack.py]
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2024-01-17 - Fix shutdown that occurs after a failed unload if curr_lane is None - Add warning if the toolhead filament sensor detects filament but the selector sensor does not - Indicate that TR_UNLOAD_TOOLHEA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
    [trad_rack.py]
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2024-01-19 Fix missing change for d4e04db
    [trad_rack.py]
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2024-02-28 Fix Set_Slicer_Unload_Preset macro (it previously failed to modify any variables in the Slicer_Unload macro)
    [trad_rack_optional.cfg]
2024-03-03 Update for wiring kit option: - update right carriage to mount breakout board - add spacer for base distribution board - update BOM calculator - update STLs readme - add eDrawing configuration that i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
    [spacer_base_distribution_board_rev1.STL]
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2024-03-08 Make _find_replacement_lane() also check the lane on which the runout occurred (fixes case where that lane is reloaded by the user but gets ignored)
    [trad_rack.py]
2024-03-10 Make TR_LOAD_TOOLHEAD pause if the selector is not homed (instead of raising a gcode command error)
    [trad_rack.py]
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2024-03-14 First pass at allowing TR_LOAD_TOOLHEAD to look for replacement lanes when selecting by tool if the tool's default lane is empty
    [trad_rack.py]
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2024-03-23 - _load_toolhead(): add option to prevent unloading if the selector has already been loaded by find_replacement_lane() - _resume_load_toolhead(): set replacement lane as the next lane to load
    [trad_rack.py]
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2024-03-24 Add ability for TR_RESUME to handle multiple consecutive resume procedures, fixing resume behavior for the following cases: - the print is paused and the user runs a command that sets up a new resume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
    [trad_rack.py]
2024-04-03 Fix flake8 violations (F402 and E731)
    [trad_rack.py]
2024-04-03 Fix check for use_wiper when not in a print
    [trad_rack_optional.cfg]
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2024-04-06 If selector position is uncertain due to setting it via SET_ACTIVE_LANE, home during the next toolchange after unloading or when finding a replacement lane
    [trad_rack.py]
2024-04-07 Mention that Danger Klipper users can skip the module installation since the trad_rack module is now included in Danger Klipper
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2024-04-28 Add option to _find_replacement_lane() to not check the runout lane (avoids an unnecessary attempted load if the lane is already known to be empty)
    [trad_rack.py]
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2024-07-28 Fix issue from 096f6a0 that could cause min_extrude_temp to be saved as tr_last_heater_target
    [trad_rack.py]
2024-08-28 Add lip to drive gear shaft hole in right gear casing to block the shaft from sliding out (the lip on the left gear casing is now thinner to still accommodate shafts slightly longer than 20.0mm, up t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
    [gear_casing_left_x1_rev5.STL, gear_casing_left_x1_rev6.STL, gear_casing_right_x1_rev5.STL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]
2024-10-02 - Catch more specific exceptions - Replace instances of self.gcode.error with self.printer.command_error to be more consistent
    [trad_rack.py]
2024-10-02 Reset next_lane and next_tool in TR_SET_ACTIVE_LANE if a matching lane was set to active
    [trad_rack.py]
2024-10-02 Skip toolchange resume callback if the next lane or tool is already loaded to the toolhead
    [trad_rack.py]
2024-10-02 Fix mistake from de3fe7a6
    [trad_rack.py]
2024-10-02 Replace PAUSE_STATE with the pre-toolchange gcode state when pausing due to a failed toolchange (ensures RESUME brings the toolhead to the right place when it restores PAUSE_STATE, avoiding an error 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
    [trad_rack.py]
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2024-10-22 Update description for TR_RESUME since it is no longer only used after a failed load or unload
    [trad_rack.py]
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2024-12-06 Add notice about the Klipper_Stuff folder no longer being used
2024-12-12 Fix _Wait_for_Toolchange_Temp macro
    [trad_rack_optional.cfg]
2024-12-26 Change rename for ACTIVATE_EXTRUDER command
    Now complies with gcode command naming restrictions from Klipper3d/klipper@5493c60
    [trad_rack_annex_nebula_2209.cfg, trad_rack_annex_nebula_5160.cfg, trad_rack_btt_mmb.cfg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]
2025-01-01 Fix connector description
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2025-05-18 Revert "Change default for homing_axes to match Klipper3d/klipper@4aa5508"
    This reverts commit 433d9e766690e1fe42e83aba9aeb0d9ccda06691.
    [trad_rack.py]
2025-06-26 Reset lane speed when using TR_UNLOAD_TOOLHEAD by default
    [trad_rack.py]
2025-07-04 Fix resume callback issue from 6af4342
    [trad_rack.py]
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2025-10-16 Remove hasattr check from d4e04db since the rest of the TradRackToolHead constructor is no longer compatible with older versions of Klipper anyway
    [trad_rack.py]
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2025-10-22 Avoid updating next_lane and next_tool if no toolchange is executed
    [trad_rack.py]
2025-10-22 Allow updating tr_last_heater_target from a redundant toolchange command
    (This may be useful if for example the user uses a toolchange command to switch to a lower-temperature material but doesn't want to bother specifying MIN_TEMP, and then they run a print where the correct MIN_TEMP for that material is specified in a toolchange command in the start gcode)
    [trad_rack.py]
2025-11-06 Only disable the selector motor if TR_HOME fails
    [trad_rack.py]
2026-01-07 _unload_selector(): don't attempt to reload missing filament if the filament is being ejected
    (the reload is meant to ensure the filament being unloaded is ready for a future load, but this is irrevelant when ejecting unusable filament e.g. after a runout)
    [trad_rack.py]
2026-01-07 Revert "_unload_selector(): don't attempt to reload missing filament if the filament is being ejected"
    This reverts commit 69450c4aae9dfe85fec84f71fe56d157ddebd610.
    [trad_rack.py]
2026-01-29 Make compatible with Klipper3d/klipper@2b4c55f
    Fixes an issue with the set_servo() function in TradRackServo no longer working due to changes to _set_pwm() in PrinterServo. set_servo() now calls _set_pwm() indirectly through the servo's GCodeRequestQueue object, similarly to what cmd_SET_SERVO() now does with Klipper3d/klipper@28995a8.
    [trad_rack.py]
